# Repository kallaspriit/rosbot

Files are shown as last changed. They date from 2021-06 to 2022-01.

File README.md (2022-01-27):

# ROSBOT

ROS 2 based robot learning platform.

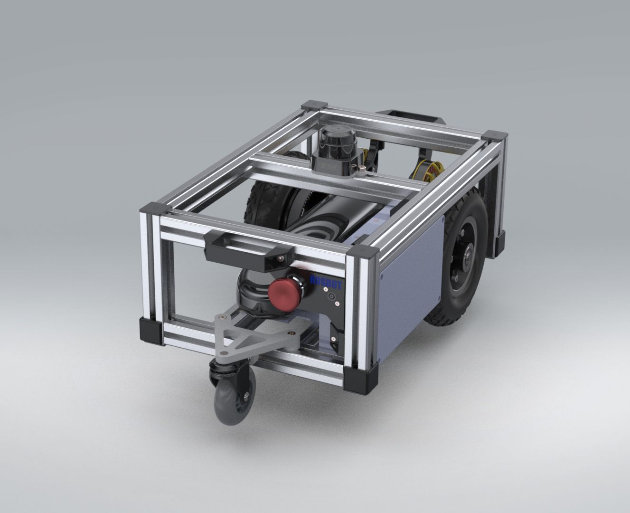
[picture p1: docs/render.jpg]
ROSBOT introductory video (https://www.youtube.com/watch?v=t-1GAfGHRLs)


_Click the image to video showing robot design and navigation in action_

## Bill of Materials

The BOM has not been designed for easy replication but most all used components and alternatives considered are there with respective links of where were they purchased so maybe it helps someone putting together a similar build :)

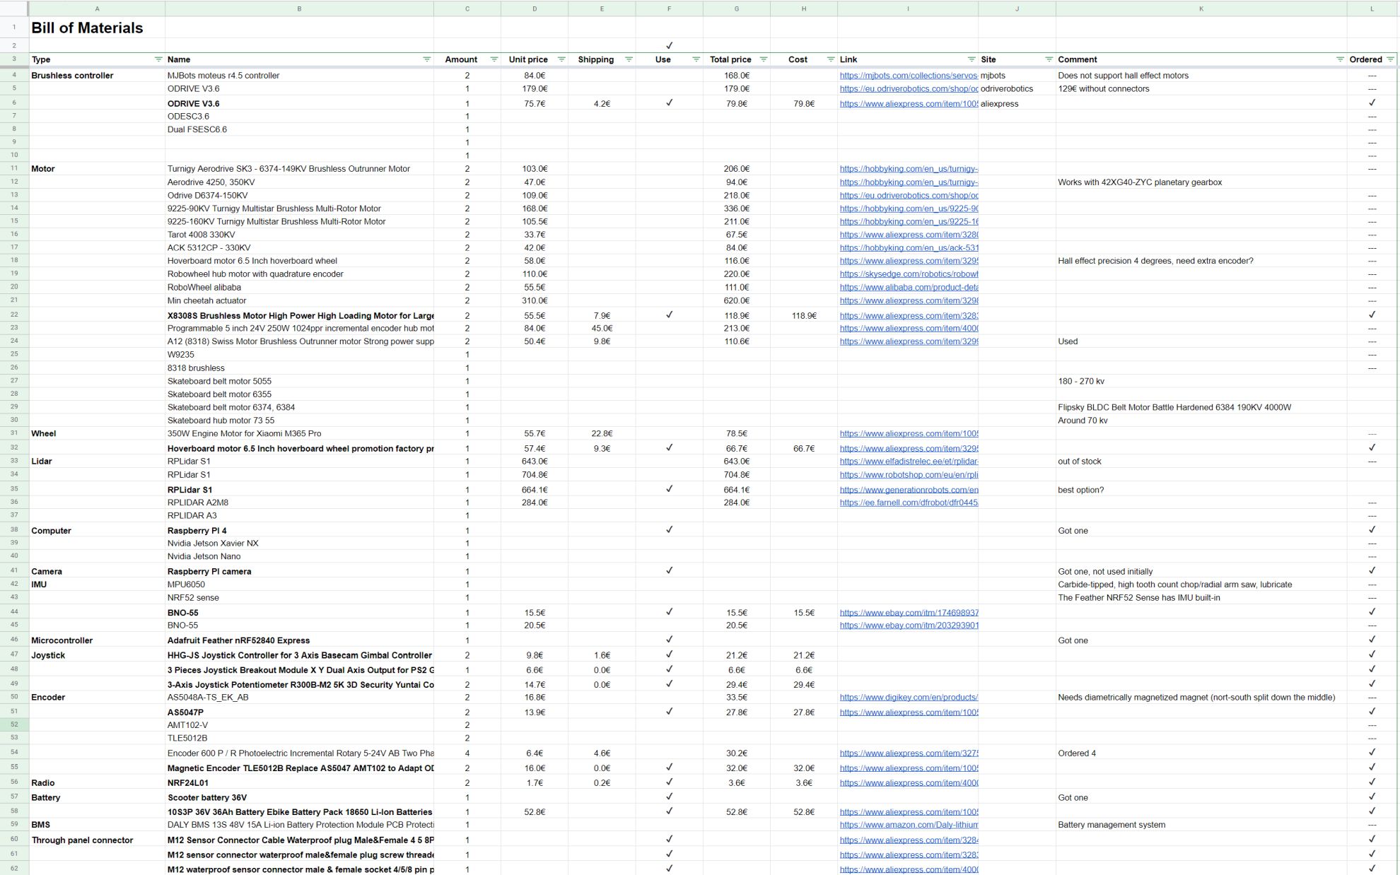
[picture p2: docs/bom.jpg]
Bill of materials (https://docs.google.com/spreadsheets/d/122i1k6gkCbc3--f4KSbXqv0-GW25-VVfwCtphQCVFGo/edit?usp=sharing)


_Click the image to open BOM_

## Run main rosbot/ros workspace

**Disclaimer**

_The following documentation is various commands and information that I've written over the time the robot was in development and everything is not up to date or relevant but maybe it helps someone._

- Add user to usb serial and input groups
  - `sudo usermod -a -G input ubuntu`
  - `sudo usermod -a -G dialout ubuntu`
  - `sudo usermod -a -G tty ubuntu`
- Build rosbot (on both the robot and the remote PC)
  - `cd ~/rosbot/ros` to open workspace
  - `rosdep install -i --from-path src --rosdistro foxy -y` to install dependencies
  - `git pull && colcon build` to pull changes and build workspace
- Launch rosbot on the robot
  - First build it if there have been any changes
  - Open new terminal
  - `cd ~/rosbot/ros` to open workspace
  - `. install/local_setup.bash` to load workspace overlay (on both robot and remote pc)
  - `ros2 launch odrive_bringup rosbot.launch.py` to launch rosbot (run on robot)
  - `ros2 launch odrive_bringup rviz.launch.py` to launch rviz (run on remote pc)
- Run joystick teleop
  - Open new terminal
  - `. install/local_setup.bash` to load workspace overlay
  - `ros2 launch teleop_twist_joy teleop.launch.py joy_config:='rosbot_xbox_bluetooth' cmd_vel:=/diff_drive_controller/cmd_vel_unstamped` to launch joystick teleop
  - Hold down left trigger (button 6) and use left and right joysticks to control speed and rotation
  - Hold down right trigger (button 7) for boost (faster movements)
- Launch odrive manual control (for testing only)
  - Open new terminal
  - `. install/local_setup.bash` to load workspace overlay
  - `ros2 launch odrive_bringup odrive.launch.py` to launch odrive test ()
  - `ros2 topic pub -r 100 /left_wheel_joint_velocity_controller/commands std_msgs/Float64MultiArray "data: [1]"`
  - `ros2 topic pub -r 100 /right_wheel_joint_velocity_controller/commands std_msgs/Float64MultiArray "data: [-1]"`
  - `ros2 launch teleop_twist_joy teleop.launch.py joy_config:='rosbot_xbox_bluetooth' cmd_vel:=/diff_drive_controller/cmd_vel_unstamped` to launch joystick teleop
  - Hold down left trigger (button 6) and use left and right joysticks to control speed and rotation
- Launch usb xbox joystick teleop that publishes to `/cmd_vel`
  - `ros2 launch teleop_twist_joy teleop.launch.py cmd_vel:=cmd_vel joy_config:=rosbot_xbox_usb`

## Debugging

- Debugging
- `ros2 topic echo /joint_states` to show joint states including velocity etc
- `ros2 topic echo /dynamic_joint_states` to show dynamic joint states including axis error etc
- `ros2 run tf2_tools view_frames.py` to generate `frames.pdf` frame tree
- `rqt` to open RQT, add plugins such as `Topics > Topic Monitor`
- `ros2 run xacro xacro ./src/rosbot_description/urdf/rosbot.urdf.xacro` to debug what's wrong with URDF file
- `ros2 run tf2_ros tf2_echo odom base_link` to verify transforms from odom to base_link
  - At time 1634580767.596875940
    - Translation: [6.986, -2.328, 0.000]
    - Rotation: in Quaternion [0.000, 0.000, -0.210, 0.978]
  - At time 1634580768.594622939
    - Translation: [7.108, -2.383, 0.000]
    - Rotation: in Quaternion [0.000, 0.000, -0.213, 0.977]

## Joystick teleop

- https://index.ros.org/p/teleop_twist_joy/github-ros2-teleop_twist_joy/
- https://github.com/ros2/teleop_twist_joy/tree/foxy/
- http://wiki.ros.org/joy
- https://github.com/medusalix/xow need xow to use xbox bluetooth controller
- Configure XOW to use xbox controller over bluetooth
  - `sudo apt install cabextract` to install dependencies
  - `git clone https://github.com/medusalix/xow`
  - `cd xow`
  - `make BUILD=RELEASE`
  - `sudo make install`
  - `sudo systemctl enable xow`
  - `sudo systemctl start xow`
  - `sudo systemctl kill -s SIGUSR1 xow` to enable XOW pairing mode (generally not needed)
- Disable ERTM
  - `sudoedit /sys/module/bluetooth/parameters/disable_ertm`
  - replace `N` with `Y`
  - reboot
- Restart bluetooth
  - `sudo service bluetooth restart`
  - `sudo rmmod btusb`
- Test controller
  - `jstest /dev/input/js0`
- Also disable ERTM permanently
  - https://www.addictivetips.com/ubuntu-linux-tips/xbox-one-controllers-over-bluetooth-linux/
  - `sudo apt install dkms git linux-headers-`uname -r``
  - `git clone https://github.com/atar-axis/xpadneo.git`
  - `cd xpadneo`
  - `sudo ./install.sh`
  - reboot
- Disable internal bluetooth when using dongle
  - `sudoedit /boot/firmware/usrcfg.txt`
  - add line `dtoverlay=disable-bluetooth`
  - reboot
  - check with `hciconfig -a` and `hcitool dev`
  - does not seem to actually work..
- Connect to bluetooth xbox controller using terminal (on robot)
  - https://simpleit.rocks/linux/shell/connect-to-bluetooth-from-cli/
  - https://raspberrypi.stackexchange.com/questions/114586/rpi-4b-bluetooth-unavailable-on-ubuntu-20-04
  - https://www.makeuseof.com/manage-bluetooth-linux-with-bluetoothctl/
  - `sudo apt install bluez pi-bluetooth joystick`
  - Append "include btcfg.txt" to `sudoedit /boot/firmware/usrcfg.txt`
  - reboot
  - `hciconfig -a` or `hcitool dev` (from bluez) to check for bluetooth devices
  - `bluetoothctl` to run interactive bluetooth controller
  - `scan on`
  - wait for xbox controller (make it pair by holding the pair button, starts to blink rapidly)
  - `trust XX:XX:XX:XX:XX:XX` to trust the controller
  - `connect XX:XX:XX:XX:XX:XX` to connect to the controller
  - `sudo chmod a+rw /dev/input/js0` to give everyone read-write permissions to joystick
  - `sudo chmod a+rw /dev/input/event4` to give everyone read-write permissions to joystick (sometimes it's one of eventX)
- If the joystick `/dev/input/eventX` does not have correct permissions then (this does not seem to actually work)
  - `sudo apt install input-utils` to install `lsinput` tool
  - `sudo lsinput` to get list of inputs, note the vendor and product of "Xbox Wireless Controller"
  - `sudoedit 80-xbox-controller.rules`
  - add `KERNEL=="event*", ATTRS{idProduct}=="02e0", ATTRS{idVendor}=="045e", MODE="0666"` etc that mathes vendor and product
- Test joystick from terminal
  - `sudo apt install joystick`
  - `jstest /dev/input/js0`
  - `ros2 run joy joy_enumerate_devices`
- Test joystick visually
  - `sudo apt install jstest-gtk`
  - `jstest-gtk`
- Test joystick messages
  - `ros2 topic echo /joy`
  - `ros2 topic echo /cmd_vel`
  - `ros2 topic echo /diff_drive_controller/cmd_vel_unstamped`

## Setup Gazebo simulator

- `sudo apt install ros-foxy-gazebo-ros-pkgs`

## Setup Raspberry PI UART

- https://askubuntu.com/questions/1254376/enable-uart-communication-on-pi4-ubuntu-20-04
- Create boot configuration backups
  - `cd /boot/firmware`
  - `sudo cp usrcfg.txt usrconfig.backup.txt`
  - `sudo cp cmdline.txt cmdline.backup.txt`
- Disable console UART
  - add `enable_uart=0` to `/boot/firmware/usrcfg.txt`
  - remove `console=serial0,115200` from `/boot/firmware/cmdline.txt`
- Disable the Serial Service which used the miniUART
  - `sudo systemctl stop serial-getty@ttyS0.service`
  - `sudo systemctl disable serial-getty@ttyS0.service`
  - `sudo systemctl mask serial-getty@ttyS0.service`
- UART Pins
  - Pin 8 TXD GPIO14
  - Pin 10 RXD GPIO15

## Setup ROS2 Navigation2 Nav2

- https://navigation.ros.org/getting_started/index.html
- Install dependencies
  - `sudo apt install ros-foxy-navigation2 ros-foxy-nav2-bringup ros-foxy-cartographer ros-foxy-cartographer-ros ros-foxy-robot-localization ros-foxy-slam-toolbox ros-foxy-gazebo-ros-pkgs ros-foxy-xacro ros-foxy-slam-toolbox`
  - `sudo apt install ros-foxy-turtlebot3*` for testing on remote pc only
- Slam toolbox on the robot
  - Use snap `slam-toolbox`
  - It has optimizations in it that make it about 10x faster
- Run mapping and navigation
  - `ros2 launch slam_toolbox online_async_launch.py` to launch slam toolbox mapper
  - `ros2 launch nav2_bringup navigation_launch.py` to run navigation2

## Run navigation2_tutorials

- Clone and build `https://github.com/ros-planning/navigation2_tutorials.git`
- launch robot `ros2 launch sam_bot_description display.launch.py`
- Launch usbteleop
  - Open new terminal
  - `cd ~/rosbot/ros`
  - `. install/local_setup.bash`
  - `ros2 launch teleop_twist_joy teleop.launch.py cmd_vel:=/demo/cmd_vel joy_config:=rosbot_xbox_usb`
  - or without the /demo in modified version
- Launch slam_toolbox
  - Open new terminal
  - `ros2 launch slam_toolbox online_async_launch.py`

## Setup Arduino

- Install Arduino IDE
- Add `https://www.adafruit.com/package_adafruit_index.json` to Arduino preferences additional boards URLs
- Install board `Adafruit nRF52`
- Install `pip3 install --user adafruit-nrfutil`
- Update bootloader
  - https://learn.adafruit.com/introducing-the-adafruit-nrf52840-feather/update-bootloader
  - Double press reset to enter DFU mode
- Install Micro-XRCE-DDS Agent
  - `git clone https://github.com/eProsima/Micro-XRCE-DDS-Agent.git`
  - `cd Micro-XRCE-DDS-Agent && git checkout foxy`
  - `mkdir build && cd build`
  - `source /opt/ros/dashing/setup.bash # to share libraries with ros2`
  - `cmake ..`
  - `make`
  - `sudo make install`
  - `sudo ldconfig /usr/local/lib/`

## Update cmake

- `cmake --version`
- `sudo apt update`
- `sudo apt install -y software-properties-common lsb-release`
- `wget -O - https://apt.kitware.com/keys/kitware-archive-latest.asc 2>/dev/null | gpg --dearmor - | sudo tee /etc/apt/trusted.gpg.d/kitware.gpg >/dev/null`
- `sudo apt-add-repository "deb https://apt.kitware.com/ubuntu/ $(lsb_release -cs) main"`
- `sudo apt update`
- `sudo apt install kitware-archive-keyring`
- `sudo rm /etc/apt/trusted.gpg.d/kitware.gpg`
- `sudo apt update`
- `sudo apt install cmake`
- `cmake --version`

## Build micro-ros on MBED

- https://github.com/micro-ROS/micro_ros_mbed
- `pip3 install catkin_pkg lark-parser empy colcon-common-extensions mbed-tools`
- `sudo apt install gcc-arm-none-eabi`
- clone repo and cd into it
- `mbed-tools deploy`
- `mbed-tools compile -m LPC1768 -t GCC_ARM -f`

## Install ROS

[Installation guide](https://docs.ros.org/en/foxy/Installation/Ubuntu-Install-Debians.html).

- Enable universe (probably not needed)
  - `sudo apt install software-properties-common`
  - `sudo add-apt-repository universe`
- Add repository
  - `sudo apt update && sudo apt install curl gnupg2 lsb-release`
  - `sudo curl -sSL https://raw.githubusercontent.com/ros/rosdistro/master/ros.key -o /usr/share/keyrings/ros-archive-keyring.gpg`
- Add repository to sources list
  - `echo "deb [arch=$(dpkg --print-architecture) signed-by=/usr/share/keyrings/ros-archive-keyring.gpg] http://packages.ros.org/ros2/ubuntu $(lsb_release -cs) main" | sudo tee /etc/apt/sources.list.d/ros2.list > /dev/null`
- Install ROS
  - `sudo apt update`
  - `sudo apt install ros-foxy-desktop`
- Install autocomplete
  - `sudo apt install -y python3-argcomplete`
- Add sourcing ROS to bashrc
  - `echo "source /opt/ros/foxy/setup.bash" >> ~/.bashrc`
- Add colcom_cd to bashrc
  - `echo "source /usr/share/colcon_cd/function/colcon_cd.sh" >> ~/.bashrc`
  - `echo "export _colcon_cd_root=~/ros2_install" >> ~/.bashrc`
- Check environment variables
  - `printenv | grep -i ROS`
- Set domain id (random number between 0-101 inclusive)
  - `echo "export ROS_DOMAIN_ID=<your_domain_id>" >> ~/.bashrc`
- Test ROS (open in separate terminals)
  - `ros2 run demo_nodes_cpp talker`
  - `ros2 run demo_nodes_py listener`
- Install ros bag for data recording/playback
  - `sudo apt-get install ros-galactic-ros2bag ros-galactic-rosbag2-storage-default-plugins`

## Install tools

- Install VSCode
  - `sudo snap install --classic code`

## Install TurtleSim

- Install
  - `sudo apt install ros-foxy-turtlesim`
- Check the package installed
  - `ros2 pkg executables turtlesim`
- Start turtlesim
  - `ros2 run turtlesim turtlesim_node`
- Start teleop to control the turtle
  - `ros2 run turtlesim turtle_teleop_key`

## Install RQT

- Install rqt
  - `sudo apt update`
  - `sudo apt install ~nros-foxy-rqt*`
- Run rqt
  - `rqt`
- Add service called
  - `select Plugins > Services > Service Caller`
  - Call `/spawn` with `x=1.0, y=1.0, name='turtle2'`
- Remap control to turtle 2
  - `ros2 run turtlesim turtle_teleop_key --ros-args --remap turtle1/cmd_vel:=turtle2/cmd_vel`
- Render rtq graph
  - `rqt_graph`
  - can also add to `rtq` by `Plugins > Introspection > Nodes Graph`

## ROS Command line

- Run node
  - `ros2 run turtlesim turtlesim_node`
  - `ros2 run turtlesim turtle_teleop_key`
  - `ros2 run turtlesim turtlesim_node --ros-args --log-level WARN` to run with custom log level
- List resources
  - `ros2 node list`
  - `ros2 topic list`
  - `ros2 topic list -t` to also show message types
  - `ros2 service list`
  - `ros2 service list -t` to also show service types
  - `ros2 action list`
  - `ros2 param list`
- Get node info
  - `ros2 node info /my_turtle`
- Show data published to topic
  - `ros2 topic echo /turtle1/cmd_vel` to see velocity commands
  - `ros2 topic echo /turtle1/pose` to see changing pose
- Get topic info
  - `ros2 topic info /turtle1/cmd_vel`
- Show messsage interface
  - `ros2 interface show geometry_msgs/msg/Twist`
- Publish message to topic
  - `ros2 topic pub <topic_name> <msg_type> '<args>'` where args is in YAML syntax
  - `ros2 topic pub --once /turtle1/cmd_vel geometry_msgs/msg/Twist "{linear: {x: 2.0, y: 0.0, z: 0.0}, angular: {x: 0.0, y: 0.0, z: 1.8}}"` publishes once
  - `ros2 topic pub --rate 1 /turtle1/cmd_vel geometry_msgs/msg/Twist "{linear: {x: 2.0, y: 0.0, z: 0.0}, angular: {x: 0.0, y: 0.0, z: 1.8}}"` publishes continuosly at 1Hz
- Show how often data is published to a topic
  - `ros2 topic hz /turtle1/pose`
- Get service type info
  - `ros2 service type <service_name>`
  - `ros2 service type /clear`
- Find service by type
  - `ros2 service find <type_name>`
  - `ros2 service find std_srvs/srv/Empty`
- Show service type structure
  - `ros2 interface show <type_name>.srv` where request and response structure is separated by ---
  - `ros2 interface show std_srvs/srv/Empty.srv`
  - `ros2 interface show turtlesim/srv/TeleportAbsolute.srv`
  - `ros2 interface show turtlesim/srv/Spawn`
- Call service
  - `ros2 service call <service_name> <service_type> <arguments>`
  - `ros2 service call /clear std_srvs/srv/Empty`
  - `ros2 service call /spawn turtlesim/srv/Spawn "{x: 2, y: 2, theta: 0.2, name: ''}"`
- Get param list
  - `ros2 param list`
- Get param value
  - `ros2 param get <node_name> <parameter_name>`
  - `ros2 param get /turtlesim background_g`
- Set param value
  - `ros2 param set <node_name> <parameter_name> <value>`
  - `ros2 param set /turtlesim background_r 150`
- Dump node parameters
  - `ros2 param dump <node_name>`
  - `ros2 param dump /turtlesim`
- Start node using parameters from dumped file
  - `ros2 run <package_name> <executable_name> --ros-args --params-file <file_name>`
  - `ros2 run turtlesim turtlesim_node --ros-args --params-file ./turtlesim.yaml`
- Get list of node actions
  - `ros2 node info /turtlesim`
  - `ros2 node info /teleop_turtle`
- Get list of all actions
  - `ros2 action list`
  - `ros2 action list -t` to also show action types
- Get action info
  - `ros2 action info /turtle1/rotate_absolute`
- Get action interface info
  - `ros2 interface show turtlesim/action/RotateAbsolute`
- Call action
  - `ros2 action send_goal <action_name> <action_type> <values>`
  - `ros2 action send_goal /turtle1/rotate_absolute turtlesim/action/RotateAbsolute "{theta: 1.57}"`
  - `ros2 action send_goal /turtle1/rotate_absolute turtlesim/action/RotateAbsolute "{theta: 3.14}" --feedback` to also get feedback
- Run rqt console
  - `ros2 run rqt_console rqt_console`
- Start node
  - `ros2 run rqt_console rqt_console`
- Launch launch file
  - `ros2 topic pub -r 1 /turtlesim1/turtle1/cmd_vel geometry_msgs/msg/Twist "{linear: {x: 2.0, y: 0.0, z: 0.0}, angular: {x: 0.0, y: 0.0, z: -1.8}}"`
- Record topic to bag
  - `ros2 bag record <topic_name>` to record a topic
  - `ros2 bag record /turtle1/cmd_vel`
  - `ros2 bag record -o subset /turtle1/cmd_vel /turtle1/pose` top choose filename `subset` and record multiple topics
- Get bag info
  - `ros2 bag info <bag_file_name>`
  - `ros2 bag info subset`
- Play back bag recording
  - `ros2 bag play <bag_file_name>`
  - `ros2 bag play subset`

## Example launch file

Starts two turtlesim nodes with different namespace names and a mimic node that makes the second turtle mimic first one.

```py
from launch import LaunchDescription
from launch_ros.actions import Node

def generate_launch_description():
    return LaunchDescription([
        Node(
            package='turtlesim',
            namespace='turtlesim1',
            executable='turtlesim_node',
            name='sim'
        ),
        Node(
            package='turtlesim',
            namespace='turtlesim2',
            executable='turtlesim_node',
            name='sim'
        ),
        Node(
            package='turtlesim',
            executable='mimic',
            name='mimic',
            remappings=[
                ('/input/pose', '/turtlesim1/turtle1/pose'),
                ('/output/cmd_vel', '/turtlesim2/turtle1/cmd_vel'),
            ]
        )
    ])
```

## TMUX terminal splitter

- Install
  - `sudo apt install tmux`
- Start
  - `tmux`
- Split terminal
  - horizonal `ctrl+b %`
  - vertical `ctrl+b "`
- Manage windows
  - create `ctrl+b c`
  - close `exit`
  - rename `ctrl+b ,`
- Navigate
  - between panels `ctrl+b ARROWS`
  - between windows `ctrl+b N` where first N=0, second N=1 etc

## Base ros setup

https://docs.ros.org/en/foxy/Installation/Ubuntu-Install-Binary.html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

/opt/ros/foxy

- sudo apt install -y python3-rosdep
- rosdep update
- rosdep install --from-paths /opt/ros/foxy/share --ignore-src --rosdistro foxy -y --skip-keys "console_bridge fastcdr fastrtps osrf_testing_tools_cpp poco_vendor rmw_connextdds rti-connext-dds-5.3.1 tinyxml_vendor tinyxml2_vendor urdfdom urdfdom_headers"

## Creating workspace

https://docs.ros.org/en/foxy/Tutorials/Workspace/Creating-A-Workspace.html

- mkdir -p ~/dev_ws/src
- cd ~/dev_ws/src
- git clone https://github.com/ros/ros_tutorials.git -b foxy-devel
- rosdep install -i --from-path src --rosdistro foxy -y
- colcon build
- open new terminal to source overlay
- cd ~/dev_ws

## Build package

- create workspace directory `mkdir ros2_ws` etc
- create "src" in this directory
- copy the library/package into src
- `rosdep install -i --from-path src --rosdistro foxy -y` to install dependencies
- cd back to workspace and run `colcon build` to build the package

## Teleop robot controller

- https://github.com/ros-teleop/teleop_tools/tree/foxy-devel
- https://ubuntu.com/blog/the-teleop_tools-arrive-in-ros-2-dashing
- `ros2 run mouse_teleop mouse_teleop`
- `ros2 run mouse_teleop mouse_teleop --ros-args -r holonomic:=true`
- `ros2 topic echo /mouse_vel`

## Run experiments/test_odrive_ros2 package

- `cd ~/rosbot/experiments/test_odrive_ros2/`
- `ros2 run odrive_ros2 odrive_node`
- `ros2 service call /connect_odrive std_srvs/srv/Trigger`
- `ros2 service call /request_state odrive_interfaces/srv/AxisState "{axis: 0, state: 8}"` (not needed if started in closed loop control)
- `ros2 service call /velocity_cmd odrive_interfaces/srv/VelocityControl "{axis: 0, turns_s: 0.5}"`
- `ros2 topic echo /barrery_percentage` (typo.. and not sure of the format, returns something like 3.5)
- `ros2 topic echo /joint_state`

## RVIZ2

- https://www.stereolabs.com/docs/ros2/rviz2/

# Run experiments/test_odrive_ros2_control package

- https://ros-controls.github.io/control.ros.org/getting_started.html
- https://github.com/ros-controls/ros2_control
- https://github.com/ros-controls/ros2_controllers
- https://github.com/ros-controls/ros2_control_demos
- https://github.com/ros-controls/ros2_controllers/tree/master/diff_drive_controller
- http://wiki.ros.org/urdf
- https://github.com/ros-controls/roadmap/blob/master/design_drafts/components_architecture_and_urdf_examples.md
- https://github.com/ros-controls/ros2_control_demos/blob/master/ros2_control_demo_bringup/config/diffbot_diff_drive_controller.yaml
- https://github.com/ros-controls/ros2_control_demos/tree/master/ros2_control_demo_description/diffbot_description
- https://github.com/ros-controls/ros2_control_demos/blob/master/ros2_control_demo_bringup/launch/diffbot_system.launch.py
- https://ros-controls.github.io/control.ros.org/ros2_control/ros2controlcli/doc/userdoc.html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 CLI
- `cd ~/rosbot/experiments/test_odrive_ros2_control/`
- `sudo apt install ros-foxy-ros2-control ros-foxy-ros2-controllers`
- `ros2 launch odrive_bringup odrive.launch.py enable_joint1:=true`
- `ros2 topic pub -r 100 /joint0_velocity_controller/commands std_msgs/Float64MultiArray "data: [1]"`
- `ros2 topic pub -r 100 /joint1_velocity_controller/commands std_msgs/Float64MultiArray "data: [-1]"`

## Run ros2_control_demos

- copy repo https://github.com/ros-controls/ros2_control_demos
- create workspace folder, move demo repo folders under `src`
- `cd ros2_control_demos/`
- `rosdep install -i --from-path src --rosdistro foxy -y`
- `colcon build`
- open new terminal
- `cd ros2_control_demos/`
- `. install/local_setup.bash`
- `ros2 launch ros2_control_demo_bringup diffbot_system.launch.py start_rviz:=true`
- `ros2 control list_hardware_interfaces` to list ros control hardware interfaces
- `ros2 control list_controllers` to list ros control controllers
- publish velocity command

```
ros2 topic pub --rate 30 /diff_drive_controller/cmd_vel_unstamped geometry_msgs/msg/Twist "linear:
 x: 0.7
 y: 0.0
 z: 0.0
angular:
 x: 0.0
 y: 0.0
 z: 1.0"
```

- control with mouse_teleop, remapping /mouse_vel to /diff_drive_controller/cmd_vel_unstamped
- `ros2 run mouse_teleop mouse_teleop --ros-args -r /mouse_vel:=/diff_drive_controller/cmd_vel_unstamped`

## Open VSCode from Ubuntu explorer context menu

- Run the following in terminal
- `wget -qO- https://raw.githubusercontent.com/cra0zy/code-nautilus/master/install.sh | bash`

## Configure ssh

- `ssh-keygen -t rsa` to create ssh key in `~/.ssh` if not already present
- `cat ~/.ssh/id_rsa.pub` to get public key from computer that wants to access robot
- add the public key to robot's `~/.ssh/authorized_keys` file
- create `~/.ssh/config` file on the remote computer with contents like

```
Host rosbot
    HostName rosbot
    User ubuntu
```

- `ssh rosbot` to open ssh connection to robot using the configuration and ssh key

## Create package

cd ~/dev_ws/src
ros2 pkg create --build-type ament_cmake <package_name>
ros2 pkg create --build-type ament_cmake --node-name my_node my_package
ros2 pkg create --build-type ament_cmake --node-name talker test_chat

## Develop C++

https://github.com/ros2/rclcpp
http://docs.ros2.org/latest/api/rclcpp/
http://wiki.ros.org/std_msgs

## Develop nodejs

https://github.com/RobotWebTools/rclnodejs
https://github.com/RobotWebTools/rclnodejs-cli
http://robotwebtools.org/rclnodejs/docs/0.20.0/index.html
https://github.com/RobotWebTools/rclnodejs/tree/develop/example
npx generate-ros-messages

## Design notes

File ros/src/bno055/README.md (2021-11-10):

# A BNO05 ROS2 Package 

## Description
A ROS2 driver for the sensor IMU Bosch BNO055.

This repo was based off of [Michael Drwiega's work on the Bosch IMU Driver for ROS 1](https://github.com/mdrwiega/bosch_imu_driver)

---
## Wiring Guide

### Selecting Connection Type

The default mode is I2C.
To select UART mode connect the `3.3V` pin to the `PS1` pin.

### CP2104 USB-to-UART Bridge

When using a CP2104 USB-to-UART Bridge:

| BNO055 | CP2104 Friend |
| --- | --- |
| Vin | 5V |
| GND | GND |
| SDA | RXD |
| SCL | TXD |

**NOTE: on the CP2104 the pins above refer to the FTDI pins at the opposite end from the USB connector

---
## ROS Node Parameters

To configure with your own settings please adjust the [node parameter file](bno055/params/bno055_params.yaml) and pass it
as an argument when starting the node:

```
ros2 run bno055 bno055 --ros-args --params-file ./src/bno055/bno055/params/bno055_params.yaml
```

### UART Connection

- **connection_type=uart**: Defines UART as sensor connection type; default='uart'
- **uart_port**: The UART port to use; default='/dev/ttyUSB0'
- **uart_baudrate**: The baud rate to use; default=115200
- **uart_timeout**: The timeout for UART transmissions in seconds to use; default=0.1
  
### Sensor Configuration

- **frame_id**: coordinate frame id of sensor default='bno055'
- **baudrate**: baudrate of sensor default=115200
- **data_query_frequency**: frequency (HZ) to read and publish data from sensor; default=100 Hz
- **calib_status_frequency**: frequency (HZ) to read and publish calibration status data from sensor; default=0.1 Hz
- **placement_axis_remap**: The sensor placement configuration (Axis remapping) defines the position and orientation of the sensor mount.
See Bosch BNO055 datasheet section "Axis Remap" for valid positions: "P0", "P1" (default), "P2", "P3", "P4", "P5", "P6", "P7".   

### ROS Topic Prefix

- **ros_topic_prefix**: ROS topic prefix to be used. Will be prepended to the default topic names (see below). Default="bno055/"

---
## ROS Topics

ROS topics published by this ROS2 Node: 

  - **bno055/imu** [(sensor_msgs/Imu)](http://docs.ros.org/api/sensor_msgs/html/msg/Imu.html)
  - **bno055/imu_raw** [(sensor_msgs/Imu)](http://docs.ros.org/api/sensor_msgs/html/msg/Imu.html)
  - **bno055/temp** [(sensor_msgs/Temperature)](http://docs.ros.org/api/sensor_msgs/html/msg/Temperature.html); The sensor's ambient temperature
  - **bno055/mag** [(sensor_msgs/MagneticField)](http://docs.ros.org/api/sensor_msgs/html/msg/MagneticField.html)
  - **bno055/calib_status** [(std_msgs/String)](http://docs.ros.org/en/api/std_msgs/html/msg/String.html) : 
  Sensor Calibration Status as JSON string - e.g. `{"sys": 3, "gyro": 3, "accel": 0, "mag": 3}`

While _bno055_ is the default ROS topic prefix, it can be configured by following the directions above.

---
  
## Development Workspace Setup

### On a Remote Device
Setup of a ROS2 workspace & IDE for a remote device (for example Raspberry Pi):

#### Clone & Build

Create a ROS2 [workspace](https://index.ros.org/doc/ros2/Tutorials/Workspace/Creating-A-Workspace/) on your remote device - for instance `~/ros2_ws`

Make sure you sourced your ROS2 installation (underlay).

Then clone the project into your workspace's src directory:

    cd ~/ros2_ws/src
    git clone https://github.com/flynneva/bno055.git
    
Perform a build of your workspace
    
    cd ~/ros2_ws
    colcon build

#### Integrate in your IDE

In order to work with the sources in your remote workspace and to integrate them in your IDE, use `sshfs`:

    sudo apt-get install sshfs
    sudo modprobe fuse

Create a IDE project directory and mount the remote ROS2 workspace:

    mkdir -p ~/projects/bno055/ros2_ws
    sshfs ubuntu@192.168.2.153:~/ros2_ws ~/projects/bno055/ros2_ws
    
Create a new project in your IDE from existing sources in `~/projects/bno055/ros2_ws`. 
You can now manipulate the remote ROS2 workspace using your local IDE (including git operations). 

### Running the ROS2 node
Run the `bno055` ROS2 node with default parameters:

    # source your local workspace (overlay) in addition to the ROS2 sourcing (underlay):
    source ~/ros2_ws/install/setup.sh
    # run the node:
    ros2 run bno055 bno055
    
Run with customized parameter file:

    ros2 run bno055 bno055 --ros-args --params-file ./src/bno055/bno055/params/bno055_params.yaml
    
### Performing flake8 Linting

To perform code linting with [flake8](https://gitlab.com/pycqa/flake8) just perform:

    cd ~/ros2_ws/src/bno055
    ament_flake8

See [www.flake8rules.com](https://www.flake8rules.com/) for more detailed information about flake8 rules.

**Note:** we take advantage of [flake8's noqa mechanisim](https://flake8.pycqa.org/en/3.1.1/user/ignoring-errors.html) to selectively ignore some errors. Just search for `# noqa:` in the source code to find them.

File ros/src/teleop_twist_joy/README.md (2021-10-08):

ros2/teleop_twist_joy
================

# Overview
The purpose of this package is to provide a generic facility for tele-operating Twist-based ROS2 robots with a standard joystick. 
It converts joy messages to velocity commands.

This node provides no rate limiting or autorepeat functionality. It is expected that you take advantage of the features built into [joy](https://index.ros.org/p/joy/github-ros-drivers-joystick_drivers/#foxy) for this.

## Executables
The package comes with the `teleop_node` that republishes `sensor_msgs/msg/Joy` messages as scaled `geometry_msgs/msg/Twist` messages.

## Subscribed Topics
- `joy (sensor_msgs/msg/Joy)`
  - Joystick messages to be translated to velocity commands.

## Published Topics
- `cmd_vel (geometry_msgs/msg/Twist)`
  - Command velocity messages arising from Joystick commands.

## Parameters
- `require_enable_button (bool, default: true)`
  - Whether to require the enable button for enabling movement.

- `enable_button (int, default: 0)`
  - Joystick button to enable regular-speed movement.
  
- `enable_turbo_button (int, default: -1)`
  - Joystick button to enable high-speed movement (disabled when -1).

- `axis_linear.<axis>`
  - Joystick axis to use for linear movement control.
  - `axis_linear.x (int, default: 5)`
  - `axis_linear.y (int, default: -1)`
  - `axis_linear.z (int, default: -1)`

- `scale_linear.<axis>`
  - Scale to apply to joystick linear axis for regular-speed movement.
  - `scale_linear.x (double, default: 0.5)`
  - `scale_linear.y (double, default: 0.0)`
  - `scale_linear.z (double, default: 0.0)`

- `scale_linear_turbo.<axis>`
  - Scale to apply to joystick linear axis for high-speed movement.
  - `scale_linear_turbo.x (double, default: 1.0)`
  - `scale_linear_turbo.y (double, default: 0.0)`
  - `scale_linear_turbo.z (double, default: 0.0)`

- `axis_angular.<axis>`
  - Joystick axis to use for angular movement control.
  - `axis_angular.yaw (int, default: 2)`
  - `axis_angular.pitch (int, default: -1)`
  - `axis_angular.roll (int, default: -1)`
  
- `scale_angular.<axis>`
  - Scale to apply to joystick angular axis.
  - `scale_angular.yaw (double, default: 0.5)`
  - `scale_angular.pitch (double, default: 0.0)`
  - `scale_angular.roll (double, default: 0.0)`
  
- `scale_angular_turbo.<axis>`
  - Scale to apply to joystick angular axis for high-speed movement.
  - `scale_angular_turbo.yaw (double, default: 1.0)`
  - `scale_angular_turbo.pitch (double, default: 0.0)`
  - `scale_angular_turbo.roll (double, default: 0.0)`

# Usage

## Install
For most users building from source will not be required, execute `apt-get install ros-<rosdistro>-teleop-twist-joy` to install.

## Run
A launch file has been provided which has three arguments which can be changed in the terminal or via your own launch file.
To configure the node to match your joystick a config file can be used. 
There are several common ones provided in this package (atk3, ps3-holonomic, ps3, xbox, xd3), located here: https://github.com/ros2/teleop_twist_joy/tree/eloquent/config.

PS3 is default, to run for another config (e.g. xbox) use this:
````
ros2 launch teleop_twist_joy teleop.launch.py joy_config:='xbox'
````

__Note:__ this launch file also launches the `joy` node so do not run it separately.

## Arguments
- `joy_config (string, default: 'ps3')`
  - Config file to use
- `joy_dev (string, default: 'dev/input/js0')`
  - Joystick device to use
- `config_filepath (string, default: '/opt/ros/<rosdistro>/share/teleop_twist_joy/config/' + LaunchConfig('joy_config') + '.config.yaml')`
  - Path to config files

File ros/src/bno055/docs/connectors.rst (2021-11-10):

connectors
====================================

.. automodule:: bno055.connectors.Connector
    :members:
    :show-inheritance:

.. automodule:: bno055.connectors.uart
    :members:
    :show-inheritance:

.. automodule:: bno055.connectors.i2c
    :members:
    :show-inheritance:

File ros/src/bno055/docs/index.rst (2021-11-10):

.. bno055 documentation master file, created by
   sphinx-quickstart on Mon Feb  8 19:58:23 2021.
   You can adapt this file completely to your liking, but it should at least
   contain the root `toctree` directive.

Welcome
==================================

A ROS2 driver for the sensor IMU Bosch BNO055.

.. toctree::
   :maxdepth: 4
   :caption: Contents:

   bno055
   connectors
   error_handling
   params
   sensor
   registers 

Indices and tables
==================

* :ref:`genindex`
* :ref:`modindex`
* :ref:`search`

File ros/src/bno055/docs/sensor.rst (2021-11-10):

sensor
====================================

.. automodule:: bno055.sensor.SensorService
    :members:

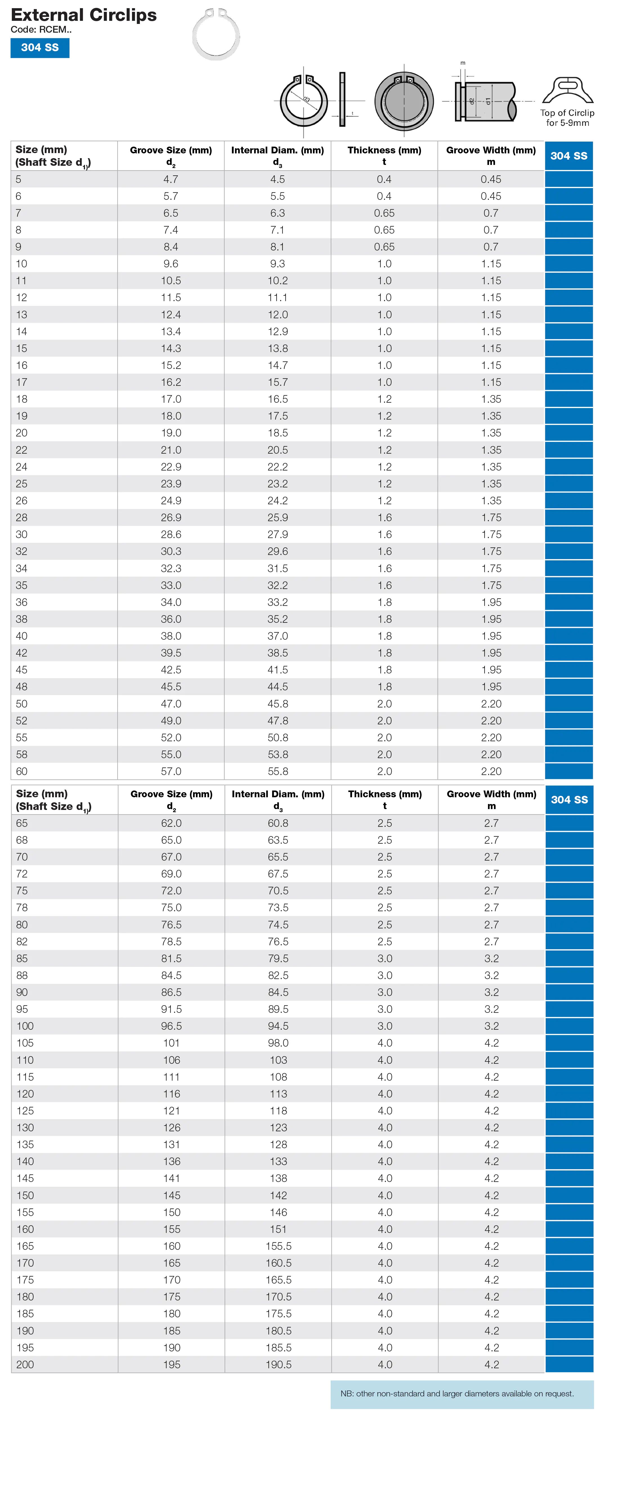
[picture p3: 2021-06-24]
docs/circlips.jpg

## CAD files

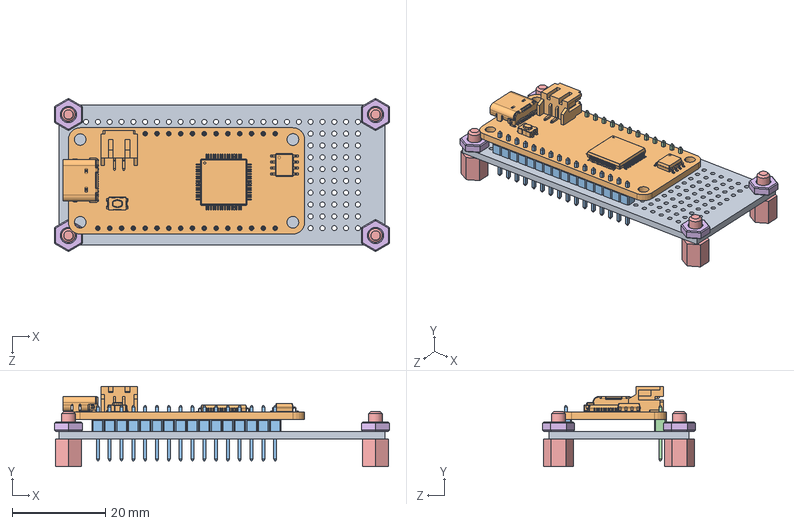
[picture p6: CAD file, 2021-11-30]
solidworks/adafruit-feather/feather-with-protoboard.SLDASM
72.0 x 17.3 x 32.9 mm
protoboard-70x30
adafruit-feather
16-Pin Header - Male - 2.54mm(2)^16-Pin Header - Male - 2.54mm(2)_pinheader-2.54mm-male-16
12-Pin Header - Male - 2.54mm(2)^12-Pin Header - Male - 2.54mm(2)_pinheader-2.54mm-male-12
spacer-nylon-6mm-M3 x 4
nut-M3 x 4

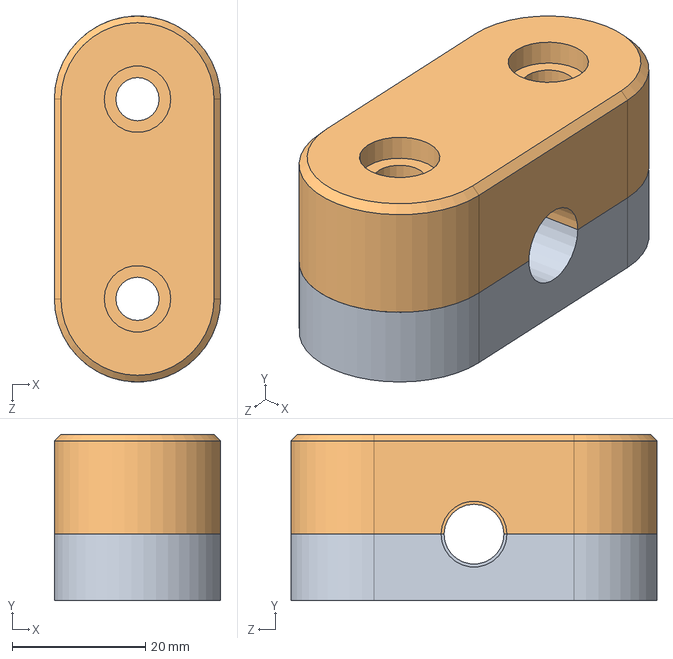
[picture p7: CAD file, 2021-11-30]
solidworks/axle-mount/axle-mount.SLDASM
25.0 x 25.0 x 55.0 mm
axle-mount-bottom
axle-mount-top

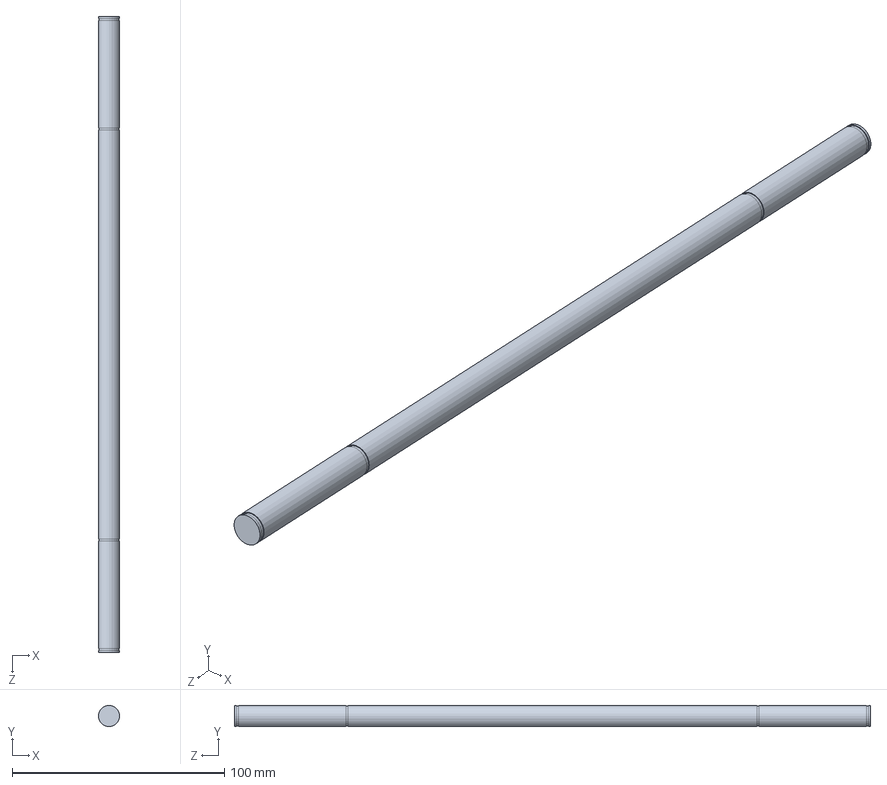
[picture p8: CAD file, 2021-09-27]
solidworks/axle/main-wheels-axle.SLDPRT
10.0 x 10.0 x 300.0 mm

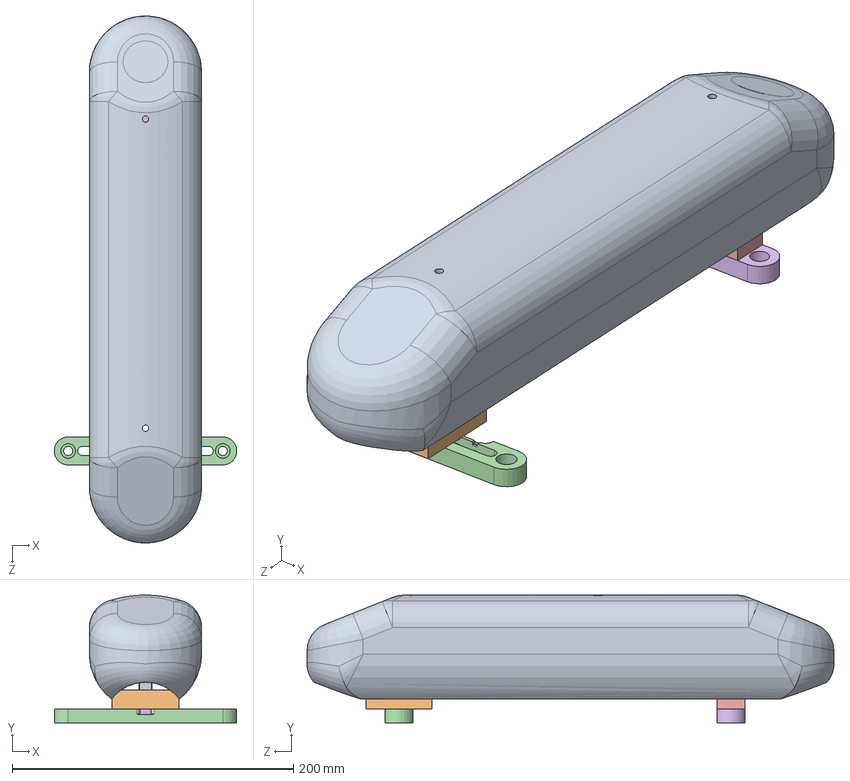
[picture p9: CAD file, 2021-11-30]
solidworks/battery/ninebot-battery.SLDASM
129.9 x 91.0 x 375.0 mm
ninebot-battery
ninebot-battery-connector
ninebot-battery-support
ninebot-battery-mount
ninebot-battery-base
ninebot-battery-base-mount

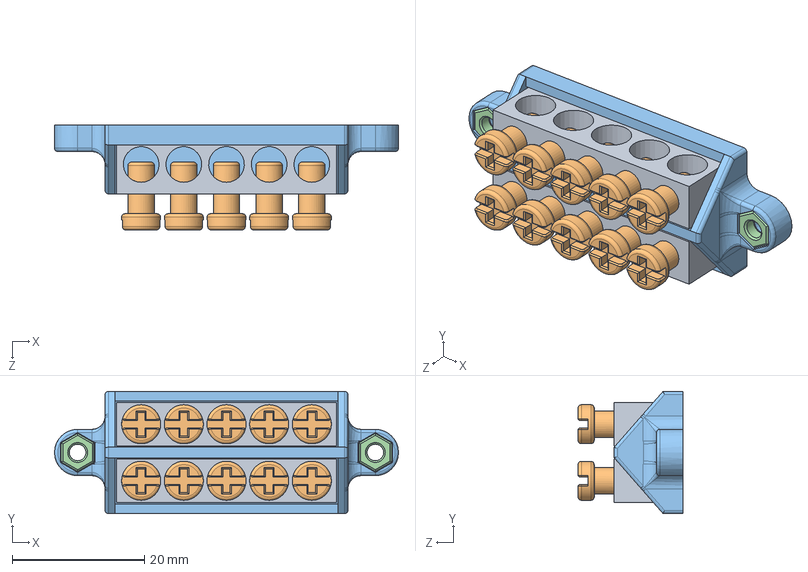
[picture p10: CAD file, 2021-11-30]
solidworks/bus-bar/bus-bar-dual-with-mount.SLDASM
52.0 x 18.5 x 15.9 mm
bus-bar-body x 2
bus-bar-screw x 10
bus-bar-dual-mount
nut-M2.5 x 2

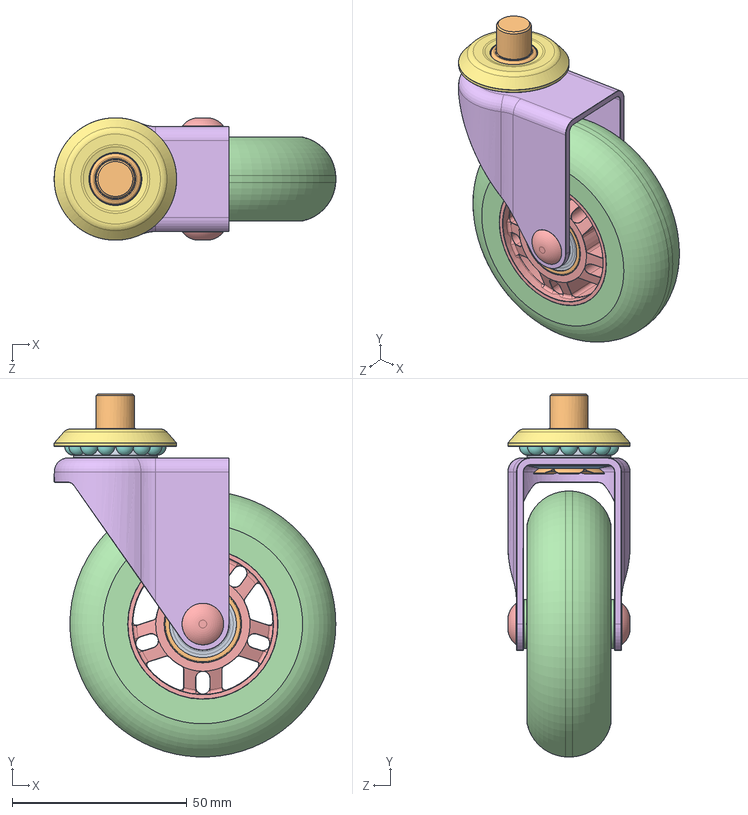
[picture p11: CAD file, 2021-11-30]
solidworks/caster-wheel/caster-wheel.SLDASM
80.5 x 103.8 x 35.0 mm
SKF_608-2Z_PART1^SKF_608-2Z_OCW_00(2)_caster-wheel x 2
SKF_608-2Z_PART2^SKF_608-2Z_OCW_00(2)_caster-wheel x 2
SKF_608-2Z_PART3^SKF_608-2Z_OCW_00(2)_caster-wheel x 14
OCW_01^OCW_00(2)_caster-wheel
OCW_02^OCW_00(2)_caster-wheel
OCW_03^OCW_00(2)_caster-wheel
OCW_05^OCW_00(2)_caster-wheel
OCW_04^OCW_00(2)_caster-wheel x 14
OCW_06^OCW_00(2)_caster-wheel
OCW_07^OCW_00(2)_caster-wheel
OCW_08^OCW_00(2)_caster-wheel
OCW_10^OCW_00(2)_caster-wheel x 2
OCW_11^OCW_00(2)_caster-wheel

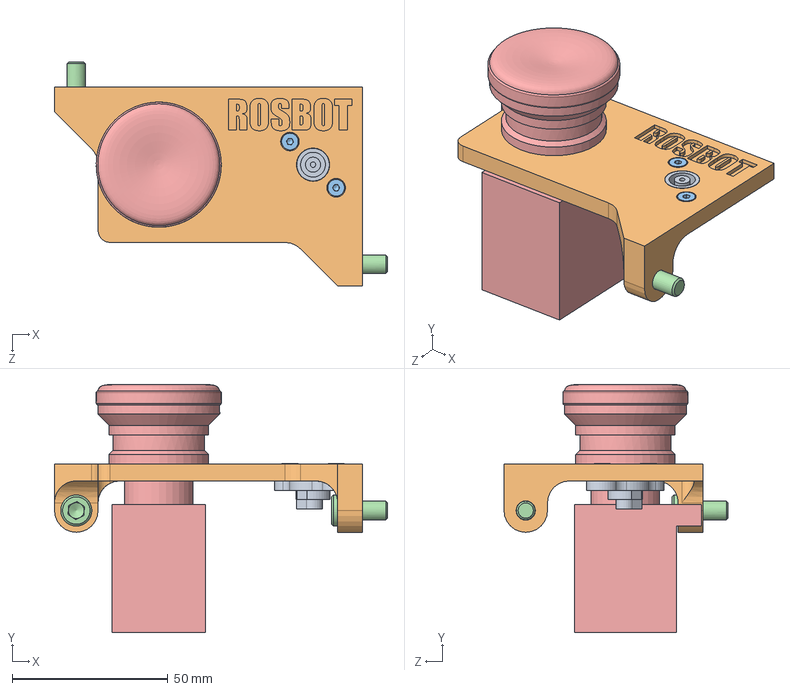
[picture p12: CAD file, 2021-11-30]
solidworks/charge-port/charge-port.SLDASM
107.0 x 79.7 x 72.0 mm
charge-port
charge-port-mount
socket countersunk head screw_am x 2
socket head cap screw_am x 2
e-stop

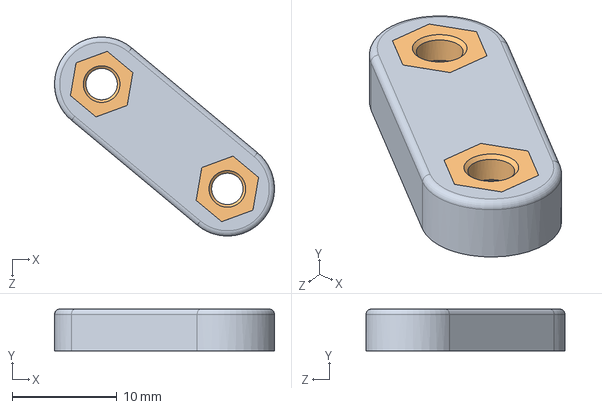
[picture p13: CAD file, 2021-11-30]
solidworks/corner-mount/corner-mount-backing.SLDASM
21.0 x 4.00 x 19.0 mm
corner-mount-backing
nut-M3 x 2

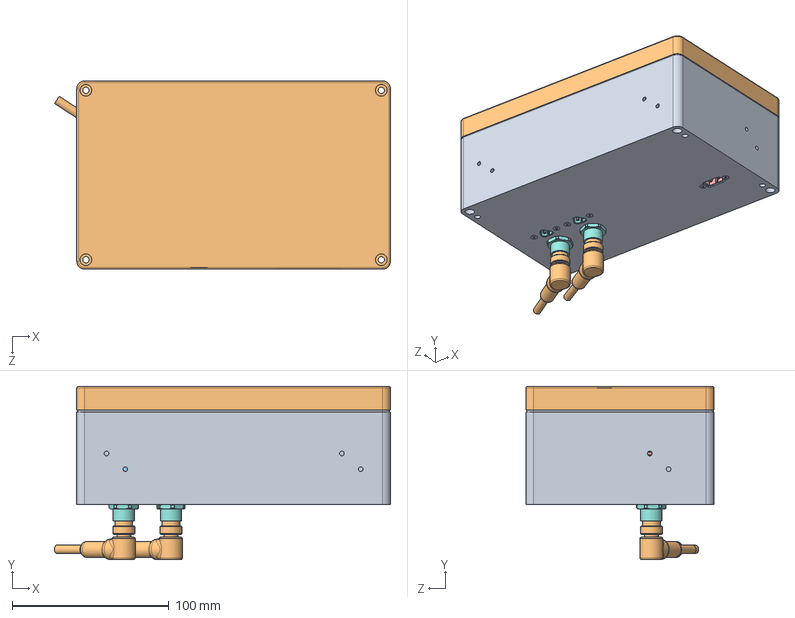
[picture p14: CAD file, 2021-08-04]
solidworks/electronics-box/electronics-box.SLDASM
214.2 x 110.4 x 120.1 mm
multicomp-G373-bottom
Board^odrive
CAP_Alum_Elec_Size_G^C15_PCB_v3.5(2)_odrive_v3.5
CAP_Alum_Elec_Size_G^C14_PCB_v3.5(2)_odrive_v3.5
CAP_Alum_Elec_Size_G^C13_PCB_v3.5(2)_odrive_v3.5
CAP_Alum_Elec_Size_G^C12_PCB_v3.5(2)_odrive_v3.5
CAP_Alum_Elec_Size_G^C11_PCB_v3.5(2)_odrive_v3.5
CAP_Alum_Elec_Size_G^C16_PCB_v3.5(2)_odrive_v3.5
CAP_Alum_Elec_Size_G^C17_PCB_v3.5(2)_odrive_v3.5
CAP_Alum_Elec_Size_G^C18_PCB_v3.5(2)_odrive_v3.5
spacer-nylon-12mm-M3 x 4
50w-resistor
variable-regulator
socket countersunk head screw_am x 8
M12-female-through-panel x 2
M12-connector-nut x 2
M12-male-cable x 2
M2.5 Nut v1^Amass XT60E1-M (2)_XT60E1-M
M2.5 Nut v1 (1)^Amass XT60E1-M (2)_XT60E1-M
Amass XT60E1-M^Amass XT60E1-M (2)_XT60E1-M
bolt-countersunk-M2.5 x 6
MT30-M-mount x 2
MT30-M-female x 2
nut-M2.5 x 4

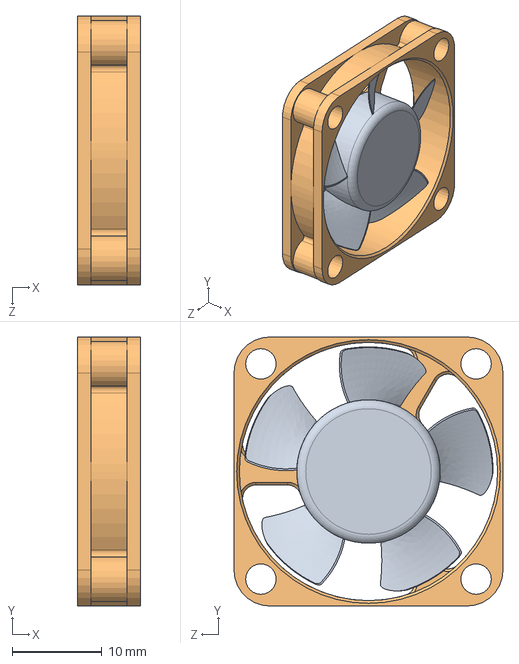
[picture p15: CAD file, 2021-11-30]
solidworks/fan/fan-30mm.SLDASM
7.00 x 30.0 x 30.0 mm
Component1^Fan 30mm(2)_fan-30mm
Fan 30mm(2)^Fan 30mm(2)_fan-30mm

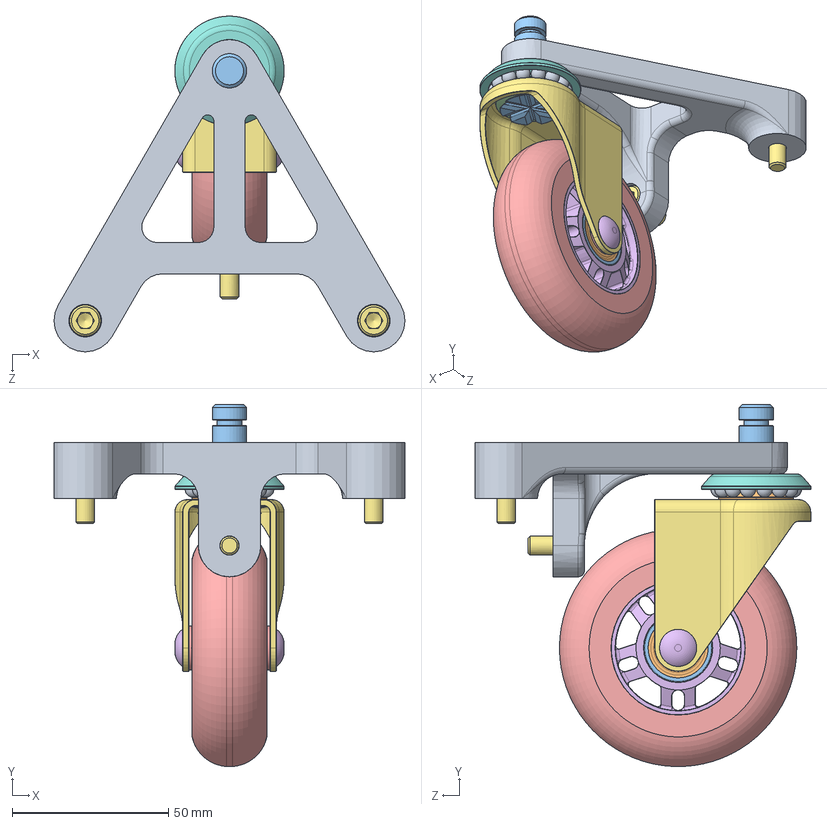
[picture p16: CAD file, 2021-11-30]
solidworks/front-wheel/front-wheel-center.SLDASM
112.4 x 115.9 x 107.5 mm
front-wheel-center-mount
SKF_608-2Z_PART1^SKF_608-2Z_OCW_00(2)_caster-wheel x 2
SKF_608-2Z_PART2^SKF_608-2Z_OCW_00(2)_caster-wheel x 2
SKF_608-2Z_PART3^SKF_608-2Z_OCW_00(2)_caster-wheel x 14
OCW_01^OCW_00(2)_caster-wheel
OCW_02^OCW_00(2)_caster-wheel
OCW_03^OCW_00(2)_caster-wheel
OCW_05^OCW_00(2)_caster-wheel
OCW_04^OCW_00(2)_caster-wheel x 14
OCW_06^OCW_00(2)_caster-wheel
OCW_07^OCW_00(2)_caster-wheel
OCW_08^OCW_00(2)_caster-wheel
OCW_10^OCW_00(2)_caster-wheel x 2
OCW_11^OCW_00(2)_caster-wheel
socket head cap screw_am x 3

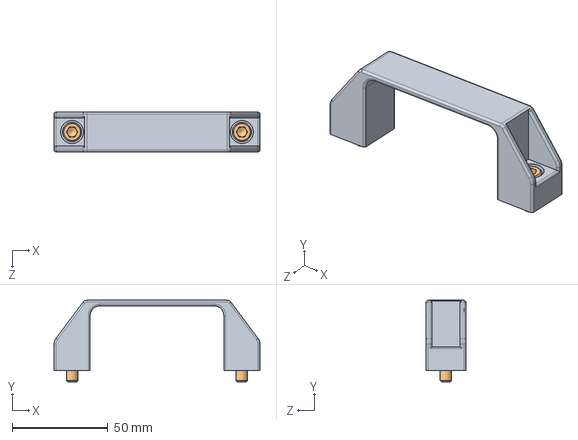
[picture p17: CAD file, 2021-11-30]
solidworks/handle/handle.SLDASM
107.3 x 42.5 x 20.6 mm
handle
socket head cap screw_am x 2

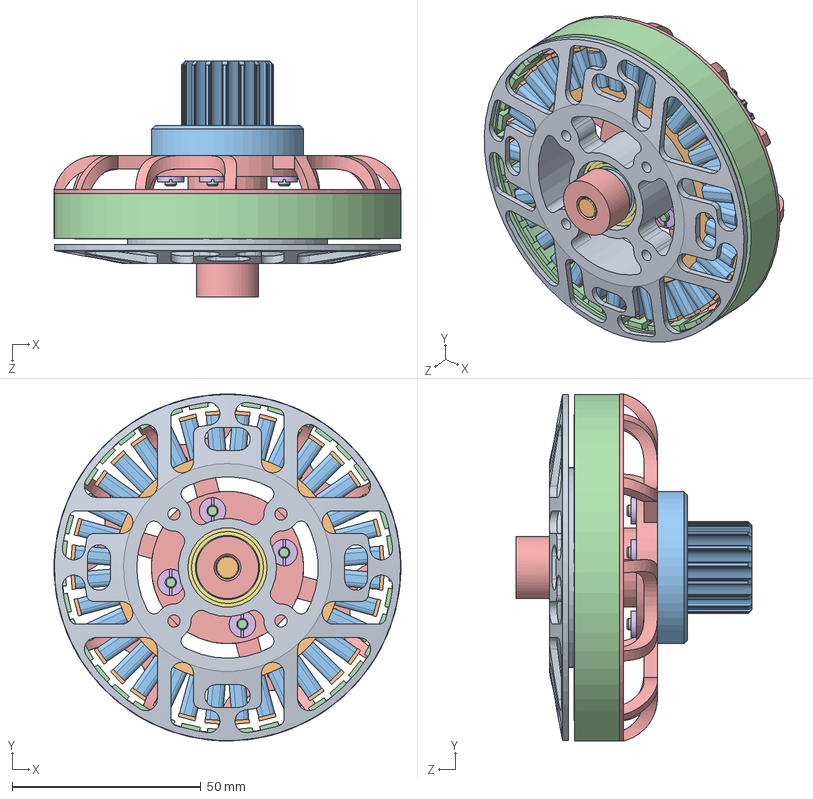
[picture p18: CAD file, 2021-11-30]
solidworks/motor/motor-X83008S.SLDASM
91.8 x 91.8 x 62.4 mm
base^motor-X83008S(2)_motor-X83008S
stator^motor-X83008S(2)_motor-X83008S
coil^motor-X83008S(2)_motor-X83008S x 36
rotor^motor-X83008S(2)_motor-X83008S
outrunner^motor-X83008S(2)_motor-X83008S
screw-mount^motor-X83008S(2)_motor-X83008S x 4
6702ZZ-bearing-15x21x4^motor-X83008S(2)_motor-X83008S x 2
shaft^motor-X83008S(2)_motor-X83008S
Part2^motor-X83008S(2)_motor-X83008S
encoder-magnet-6025
motor-pulley-HTD-5M-16
socket countersunk head screw_am x 4
motor-magnet-mount

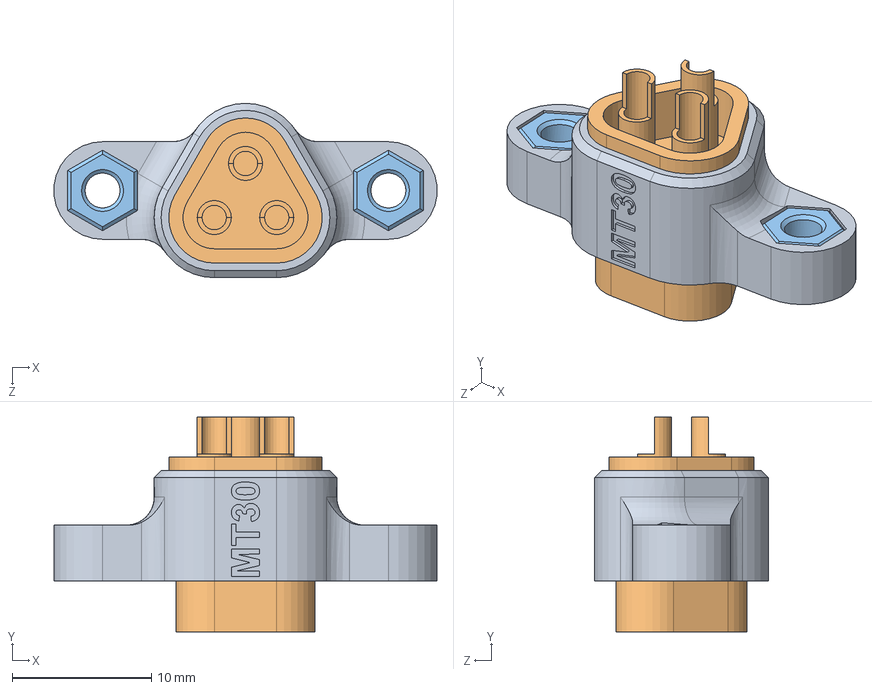
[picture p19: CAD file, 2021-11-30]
solidworks/MT30-M/MT30-with-mount.SLDASM
27.5 x 15.4 x 12.5 mm
MT30-M-mount
MT30-M-female
nut-M2.5 x 2

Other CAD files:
solidworks/multicomp-G373/multicomp-G373.SLDASM
solidworks/odrive/odrive.SLDASM
solidworks/pinheader/pinheader-2.54mm-female-20.SLDASM
solidworks/raspberry-pi-4/rpi-with-cooler.SLDASM
solidworks/50w-resistor/50w-resistor.SLDPRT
solidworks/M12-connector/M12-connector-nut.SLDPRT
solidworks/M12-connector/M12-female-through-panel.SLDPRT
solidworks/M12-connector/M12-male-cable.SLDPRT
solidworks/MT30-M/MT30-M-female.SLDPRT
solidworks/MT30-M/MT30-M-mount.SLDPRT
solidworks/XT60E1-M/XT60E1-M.SLDASM
solidworks/adafruit-feather/adafruit-feather.SLDPRT
solidworks/axle-mount/axle-mount-bottom.SLDPRT
solidworks/axle-mount/axle-mount-top.SLDPRT
solidworks/battery/ninebot-battery-base-mount.SLDPRT
solidworks/battery/ninebot-battery-base.SLDPRT
solidworks/battery/ninebot-battery-connector.SLDPRT
solidworks/battery/ninebot-battery-mount.SLDPRT
solidworks/battery/ninebot-battery-support.SLDPRT
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

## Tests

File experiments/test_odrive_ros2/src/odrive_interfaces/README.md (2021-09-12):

# odrive_interfaces
ROS2 interfaces for ODrive

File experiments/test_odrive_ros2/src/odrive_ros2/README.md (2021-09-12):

# odrive_ros2
ROS2 node for ODrive (Firmware version >= v0.5.1)

## Installation Instructions

### Install ODrive tools
[ODrive Docs](https://docs.odriverobotics.com/)

### Install from source
```bash
# Create workspace
mkdir -p ~/ros2_ws/src
cd ~/ros2_ws/src

# Get node
git clone https://github.com/skymaze/odrive_ros2.git

# Get interface
git clone https://github.com/skymaze/odrive_interfaces.git

# Build
cd ~/ros2_ws
colcon build
```

## Usage Instructions

### Start odrive node
```bash
source ~/ros2_ws/install/local_setup.bash
# To launch with "ros2 run"
ros2 run odrive_ros2 odrive_node
```

### Parameters

- connection.timeout
- battery.max_voltage
- battery.min_voltage
- battery.topic
- joint_state.topic

### Topics

- barrery_percentage
- joint_state

### Services

- connect_odrive
- request_state
- position_cmd
- velocity_cmd

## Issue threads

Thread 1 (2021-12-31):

This looks great! BOM?

samuk, 2021-12-31:
Hi nice work this looks like a good machine. Is there a BOM available anywhere?

grafoteka, 2022-01-27:
Hi @kallaspriit, thank you for sharing the project, it looks great!

I'm with @samuk, is available any BOM of the project? From your video I have identify these components:

- RPlidar S1 ([https://www.slamtec.com/en/Lidar/S1](https://www.slamtec.com/en/Lidar/S1))
- Brushless motor X8308S ([https://es.aliexpress.com/i/32837933318.html](https://es.aliexpress.com/i/32837933318.html))
- IMU BNO-055 ([https://tienda.bricogeek.com/medicion-inercial-imu/802-sensor-inercial-absoluto-9-dof-bno055.html](https://tienda.bricogeek.com/medicion-inercial-imu/802-sensor-inercial-absoluto-9-dof-bno055.html))
- RPI 4B
- Adafruit Feather nRF52840 Sense ([https://learn.adafruit.com/adafruit-feather-sense](https://learn.adafruit.com/adafruit-feather-sense))
- ODrive 3.6 Brushless controller [https://odriverobotics.com/shop/odrive-v36](https://odriverobotics.com/shop/odrive-v36)
- TLE5012B Magnetic Motors Encoders - I could not found with module it is.
- Belt Drive HTD 4.5:1 Gear Ratio
- 32V Battery from Segway Ninebot ES4

kallaspriit, 2022-01-27:
Hey, you've got it right. I've updated the README with link to my own complete BOM. It was not really made for easy replication but rather for myself but maybe it helps :)

Closed 2022-01-27.

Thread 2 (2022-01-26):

Motor Freely Moves when Zero Velocity is Sent

David9696, 2022-01-26:
Hi,

Thanks for sharing this great project.

I tried to implement the sharing package with my own robot. It can be run without issue.

However, when I issued an zero cmd_vel, the wheel would stop but the it is freely to rotate if I rotate it manually. Is this behavior expected? Could I make the wheel not moving or hold when zero cmd_vel is sent? Otherwise the robot would drift for a distance before it really stops.

Hope you could enlighten me.

Thanks.

kallaspriit, 2022-01-27:
Are you using ODrive as well? My robot holds position and the wheels can not be rotated when zero velocity is requested.

kallaspriit, 2022-11-07:
Closing due to inactivity.

Closed 2022-11-07.

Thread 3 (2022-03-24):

problem with  controller manager.

Gilocho, 2022-03-24:
hello I'm having problems running the package with :
`ros2 launch rosbot_bringup robot.launch.py `

stays on the line:
```
[spawner.py-4] [INFO] [1648164601.832733413] [spawner_diff_drive_controller]: Waiting for /controller_manager services
[spawner.py-3] [INFO] [1648164601.833070266] [spawner_joint_state_broadcaster]: Waiting for /controller_manager services
```

and after a few seconds mark:
```
[spawner.py-4] Traceback (most recent call last):
[spawner.py-4]   File "/opt/ros/foxy/lib/controller_manager/spawner.py", line 204, in <module>
[spawner.py-4]     sys.exit(main())
[spawner.py-4]   File "/opt/ros/foxy/lib/controller_manager/spawner.py", line 123, in main
[spawner.py-4]     if is_controller_loaded(node, controller_manager_name, controller_name):
[spawner.py-4]   File "/opt/ros/foxy/lib/controller_manager/spawner.py", line 65, in is_controller_loaded
[spawner.py-4]     controllers = list_controllers(node, controller_manager).controller
[spawner.py-4]   File "/opt/ros/foxy/lib/python3.8/site-packages/controller_manager/controller_manager_services.py", line 49, in list_controllers
[spawner.py-4]     return service_caller(node, f'{controller_manager_name}/list_controllers',
[spawner.py-4]   File "/opt/ros/foxy/lib/python3.8/site-packages/controller_manager/controller_manager_services.py", line 29, in service_caller
[spawner.py-4]     raise RuntimeError(f'Could not contact service {service_name}')
[spawner.py-4] RuntimeError: Could not contact service /controller_manager/list_controllers
[spawner.py-3] Traceback (most recent call last):
[spawner.py-3]   File "/opt/ros/foxy/lib/controller_manager/spawner.py", line 204, in <module>
[spawner.py-3]     sys.exit(main())
[spawner.py-3]   File "/opt/ros/foxy/lib/controller_manager/spawner.py", line 123, in main
[spawner.py-3]     if is_controller_loaded(node, controller_manager_name, controller_name):
[spawner.py-3]   File "/opt/ros/foxy/lib/controller_manager/spawner.py", line 65, in is_controller_loaded
[spawner.py-3]     controllers = list_controllers(node, controller_manager).controller
[spawner.py-3]   File "/opt/ros/foxy/lib/python3.8/site-packages/controller_manager/controller_manager_services.py", line 49, in list_controllers
[spawner.py-3]     return service_caller(node, f'{controller_manager_name}/list_controllers',
[spawner.py-3]   File "/opt/ros/foxy/lib/python3.8/site-packages/controller_manager/controller_manager_services.py", line 29, in service_caller
[spawner.py-3]     raise RuntimeError(f'Could not contact service {service_name}')
[spawner.py-3] RuntimeError: Could not contact service /controller_manager/list_controllers
[ERROR] [spawner.py-4]: process has died [pid 15312, exit code 1, cmd '/opt/ros/foxy/lib/controller_manager/spawner.py diff_drive_controller --ros-args'].
[ERROR] [spawner.py-3]: process has died [pid 15310, exit code 1, cmd '/opt/ros/foxy/lib/controller_manager/spawner.py joint_state_broadcaster --ros-args'].
```
directly use the library: https://github.com/Factor-Robotics/odrive_ros2_control/
and let me control the two motors without problems
any idea why this could happen?

thanks for you help

kallaspriit, 2022-11-07:
Sorry but don't know how to help you with this one. Sometimes ROS fails for no apparent reason and just restarting everything makes it work again.

Closed 2022-11-07.

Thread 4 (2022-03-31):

rplidar data frame

HusamZain, 2022-03-31:
Great work, and thank you for sharing !
I'm building the same project and using almost the same hardware you have , but I'm facing a problem with the Laserscan data that published from the rplidar package that you used ,  it's rotates with the robot when I rotate the robot, so I was wondering if you countered the same issue when you worked with rplidar?
as you can see in the pic, the laserscan data rotates when I rotate the robot, not sure is it beacouse the TF, but I have a similar urdf file as yours(odom>>base_link and base_link>>lidar_link)

kallaspriit, 2022-07-10:
Haven't had problems with the library, check your transforms :)

Closed 2022-07-10.

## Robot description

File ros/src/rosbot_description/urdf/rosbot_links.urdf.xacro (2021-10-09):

<?xml version="1.0"?>
<robot xmlns:xacro="http://www.ros.org/wiki/xacro">

  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
  <xacro:include filename="$(find rosbot_description)/urdf/inertia.urdf.xacro" />

  <xacro:macro name="rosbot_links" params="prefix">

    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
    <xacro:property name="body_mass" value="6.0" />
    <xacro:property name="body_width" value="0.46" />
    <xacro:property name="body_length" value="0.3" />
    <xacro:property name="body_height" value="0.17" />
    <xacro:property name="body_ground_offset" value="0.0575" />

    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
    <xacro:property name="lidar_height" value="0.055" />
    <xacro:property name="lidar_radius" value="0.0275" />

    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
    <xacro:property name="rear_wheel_mass" value="0.5" />
    <xacro:property name="rear_wheel_width" value="0.05" />
    <xacro:property name="rear_wheel_radius" value="0.0975" />
    <xacro:property name="rear_wheel_origin_x" value="-0.1" />
    <xacro:property name="rear_wheel_distance" value="0.241" />

    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
    <xacro:property name="front_wheel_mass" value="0.2" />
    <xacro:property name="front_wheel_width" value="0.025" />
    <xacro:property name="front_wheel_radius" value="0.0385" />
    <xacro:property name="front_wheel_origin_x" value="0.26757" />

    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
    <xacro:property name="imu_size" value="0.02" />

    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
    <xacro:property name="camera_width" value="0.025" />
    <xacro:property name="camera_length" value="0.05" />
    <xacro:property name="camera_height" value="0.025" />

    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
    <link name="${prefix}base_link"/>

    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
    <link name="base_footprint"/>
    <joint name="${prefix}base_joint" type="fixed">
      <parent link="${prefix}base_link"/>
      <child link="${prefix}base_footprint" />
      <origin xyz="${rear_wheel_origin_x * -1} 0 0" rpy="0 0 0"/>
    </joint>

    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
    <link name="${prefix}body">
      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
      <xacro:box_inertia m="${body_mass}" w="${body_width}" d="${body_length}" h="${body_height}"/>
    </link>
    <joint name="${prefix}body_joint" type="fixed">
      <parent link="${prefix}base_link"/>
      <child link="${prefix}body"/>
      <origin xyz="${-rear_wheel_origin_x} 0 ${body_ground_offset + body_height / 2}" rpy="0 0 0"/>
      <axis xyz="0 0 1"/>
    </joint>

    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
    <link name="${prefix}left_wheel">
      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
      <xacro:cylinder_inertia m="${rear_wheel_mass}" r="${rear_wheel_radius}" h="${rear_wheel_width}"/>
    </link>
    <joint name="${prefix}left_wheel_joint" type="continuous">
      <parent link="${prefix}base_link"/>
      <child link="${prefix}left_wheel"/>
      <origin xyz="0 ${rear_wheel_distance/2} ${rear_wheel_radius}" rpy="0 0 0"/>
      <axis xyz="0 1 0"/>
      <dynamics damping="0.2"/>
    </joint>

    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
    <link name="${prefix}right_wheel">
      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
      <xacro:cylinder_inertia m="${rear_wheel_mass}" r="${rear_wheel_radius}" h="${rear_wheel_width}"/>
    </link>
    <joint name="${prefix}right_wheel_joint" type="continuous">
      <parent link="${prefix}base_link"/>
      <child link="${prefix}right_wheel"/>
      <origin xyz="0 -${rear_wheel_distance/2} ${rear_wheel_radius}" rpy="0 0 0"/>
      <axis xyz="0 1 0"/>
      <dynamics damping="0.2"/>
    </joint>

    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
    <link name="${prefix}front_wheel">
      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
      <xacro:sphere_inertia m="${front_wheel_mass}" r="${front_wheel_radius}"/>
    </link>
    <joint name="${prefix}front_wheel_joint" type="fixed">
      <parent link="${prefix}body"/>
      <child link="${prefix}front_wheel"/>
      <origin xyz="${front_wheel_origin_x} 0 ${front_wheel_radius - body_height / 2 - body_ground_offset}" rpy="0 0 0"/>
      <axis xyz="0 0 1"/>
      <dynamics damping="0.2"/>
    </joint>

    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
    <link name="${prefix}base_laser">
      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
    </link>
    <joint name="${prefix}lidar_joint" type="fixed">
      <parent link="${prefix}body"/>
      <child link="${prefix}base_laser"/>
      <origin xyz="0 0 ${body_height / 2 + lidar_height / 2}" rpy="0 0 ${pi}"/>
      <axis xyz="0 0 1"/>
    </joint>

    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
    <link name="imu_link">
      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
      <xacro:cylinder_inertia m="0.01" r="${imu_size}" h="${imu_size}"/>
    </link>
    <joint name="imu_joint" type="fixed">
      <parent link="body"/>
      <child link="imu_link"/>
      <origin xyz="${rear_wheel_origin_x} 0 ${body_height / 2 + imu_size / 2}" rpy="0 0 0"/>
      <axis xyz="0 0 1"/>
    </joint>

    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
    <link name="${prefix}rgb_camera_link">
      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
    </link>
    <joint name="${prefix}camera_joint" type="fixed">
      <parent link="${prefix}body"/>
      <child link="${prefix}rgb_camera_link"/>
      <origin xyz="${body_width / 2} 0 ${body_height / 2 + camera_height / 2}" rpy="0 0 0"/>
    </joint>

    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
    <link name="depth_camera_link"/>
    <joint name="depth_camera_joint" type="fixed">
      <origin xyz="0 0 0" rpy="${-pi/2} 0 ${pi/2}"/>
      <parent link="rgb_camera_link"/>
      <child link="depth_camera_link"/>
    </joint>

  </xacro:macro>

</robot>

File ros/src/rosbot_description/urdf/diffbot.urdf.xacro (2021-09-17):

<?xml version="1.0"?>
<robot xmlns:xacro="http://www.ros.org/wiki/xacro">

  <xacro:macro name="diffbot" params="prefix">

  <!-- Constants for robot dimensions -->
  <xacro:property name="PI" value="3.1415926535897931"/>
  <xacro:property name="base_mass" value="0.3" /> <!-- arbitrary value for base mass -->
  <xacro:property name="base_width" value="0.1" />
  <xacro:property name="base_length" value="0.1" />
  <xacro:property name="base_height" value="0.05" />
  <xacro:property name="wheel_mass" value="0.3" /> <!-- arbitrary value for wheel mass -->
  <xacro:property name="wheel_len" value="0.020" />
  <xacro:property name="wheel_radius" value="0.015" />
  <xacro:property name="caster_wheel_mass" value="0.1" /> <!-- arbitrary value for caster wheel mass -->
  <xacro:property name="caster_wheel_radius" value="0.015" />
  <xacro:property name="z_offset" value="-${base_height/2}" /> <!-- Space btw top of beam and the each joint -->

  <!-- Base Link -->
  <link name="${prefix}base_link">
    <collision>
      <origin xyz="0 0 0" rpy="0 0 0"/>
      <geometry>
        <box size="${base_width} ${base_length} ${base_height}"/>
      </geometry>
    </collision>

    <visual>
      <origin xyz="0 0 0" rpy="0 0 0"/>
      <geometry>
        <box size="${base_width} ${base_length} ${base_height}"/>
      </geometry>
      <material name="orange"/>
    </visual>

    <inertial>
      <origin xyz="0 0 0" rpy="0 0 0"/>
      <mass value="${base_mass}"/>
      <inertia ixx="${base_mass / 12.0 * (base_length*base_length + base_height*base_height)}" ixy="0.0" ixz="0.0" iyy="${base_mass / 12.0 * (base_height*base_height + base_width*base_width)}" iyz="0.0" izz="${base_mass / 12.0 * (base_width*base_width + base_length*base_length)}"/>
      </inertial>
    </link>

    <joint name="${prefix}left_wheel_joint" type="continuous">
      <parent link="${prefix}base_link"/>
      <child link="${prefix}left_wheel"/>
      <origin xyz="0 -${base_width/2} ${z_offset}" rpy="0 0 0"/>
      <axis xyz="0 1 0"/>
      <dynamics damping="0.2"/>
    </joint>

    <!-- left wheel Link -->
    <link name="${prefix}left_wheel">
      <collision>
        <origin xyz="0 0 0" rpy="${PI/2} 0 0"/>
        <geometry>
          <cylinder length="${wheel_len}" radius="${wheel_radius}"/>
        </geometry>
      </collision>

      <visual>
        <origin xyz="0 0 0" rpy="${PI/2} 0 0"/>
        <geometry>
          <cylinder length="${wheel_len}" radius="${wheel_radius}"/>
        </geometry>
        <material name="black"/>
      </visual>

      <inertial>
        <origin xyz="0 0 0" rpy="${PI/2} 0 0"/>
        <mass value="${wheel_mass}"/>
        <inertia ixx="${wheel_mass / 12.0 * (3*wheel_radius + wheel_len*wheel_len)}" ixy="0.0" ixz="0.0" iyy="${wheel_mass / 12.0 * wheel_radius*wheel_radius}" iyz="0.0" izz="${wheel_mass / 12.0 * wheel_radius*wheel_radius}"/>
        </inertial>
      </link>

    <joint name="${prefix}right_wheel_joint" type="continuous">
      <parent link="${prefix}base_link"/>
      <child link="${prefix}right_wheel"/>
      <origin xyz="0 ${base_width/2} ${z_offset}" rpy="0 0 0"/>
      <axis xyz="0 1 0"/>
      <dynamics damping="0.2"/>
    </joint>

    <!-- right wheel Link -->
    <link name="${prefix}right_wheel">
      <collision>
        <origin xyz="0 0 0" rpy="${PI/2} 0 0"/>
        <geometry>
          <cylinder length="${wheel_len}" radius="${wheel_radius}"/>
        </geometry>
      </collision>

      <visual>
        <origin xyz="0 0 0" rpy="${PI/2} 0 0"/>
        <geometry>
          <cylinder length="${wheel_len}" radius="${wheel_radius}"/>
        </geometry>
        <material name="black"/>
      </visual>

      <inertial>
        <origin xyz="0 0 0" rpy="${PI/2} 0 0"/>
        <mass value="${wheel_mass}"/>
        <inertia ixx="${wheel_mass / 12.0 * (3*wheel_radius + wheel_len*wheel_len)}" ixy="0.0" ixz="0.0" iyy="${wheel_mass / 12.0 * wheel_radius*wheel_radius}" iyz="0.0" izz="${wheel_mass / 12.0 * wheel_radius*wheel_radius}"/>
        </inertial>
      </link>

    <joint name="${prefix}caster_frontal_wheel_joint" type="fixed">
      <parent link="${prefix}base_link"/>
      <child link="${prefix}caster_frontal_wheel"/>
      <origin xyz="${base_width/2 - caster_wheel_radius} 0 ${z_offset}" rpy="0 0 0"/>
    </joint>

    <!-- caster frontal wheel Link -->
    <link name="${prefix}caster_frontal_wheel">
      <collision>
        <origin xyz="0 0 0" rpy="0 0 0"/>
        <geometry>
          <sphere radius="${caster_wheel_radius}"/>
        </geometry>
      </collision>

      <visual>
        <origin xyz="0 0 0" rpy="0 0 0"/>
        <geometry>
          <sphere radius="${caster_wheel_radius}"/>
        </geometry>
        <material name="white"/>
      </visual>

      <inertial>
        <origin xyz="0 0 0" rpy="0 0 0"/>
        <mass value="${caster_wheel_mass}"/>
        <inertia ixx="${caster_wheel_mass * 0.4 * (caster_wheel_radius * caster_wheel_radius)}" ixy="0.0" ixz="0.0" iyy="${caster_wheel_mass * 0.4 * (caster_wheel_radius * caster_wheel_radius)}" iyz="0.0" izz="${caster_wheel_mass * 0.4 * (caster_wheel_radius * caster_wheel_radius)}"/>
        </inertial>
      </link>

    <joint name="${prefix}caster_rear_wheel_joint" type="fixed">
      <parent link="${prefix}base_link"/>
      <child link="${prefix}caster_rear_wheel"/>
      <origin xyz="${-base_width/2 + caster_wheel_radius} 0 ${z_offset}" rpy="0 0 0"/>
    </joint>

    <!-- caster rear wheel Link -->
    <link name="${prefix}caster_rear_wheel">
      <collision>
        <origin xyz="0 0 0" rpy="0 0 0"/>
        <geometry>
          <sphere radius="${caster_wheel_radius}"/>
        </geometry>
      </collision>

      <visual>
        <origin xyz="0 0 0" rpy="0 0 0"/>
        <geometry>
          <sphere radius="${caster_wheel_radius}"/>
        </geometry>
        <material name="white"/>
      </visual>

      <inertial>
        <origin xyz="0 0 0" rpy="0 0 0"/>
        <mass value="${caster_wheel_mass}"/>
        <inertia ixx="${caster_wheel_mass * 0.4 * (caster_wheel_radius * caster_wheel_radius)}" ixy="0.0" ixz="0.0" iyy="${caster_wheel_mass * 0.4 * (caster_wheel_radius * caster_wheel_radius)}" iyz="0.0" izz="${caster_wheel_mass * 0.4 * (caster_wheel_radius * caster_wheel_radius)}"/>
        </inertial>
      </link>

  </xacro:macro>

</robot>

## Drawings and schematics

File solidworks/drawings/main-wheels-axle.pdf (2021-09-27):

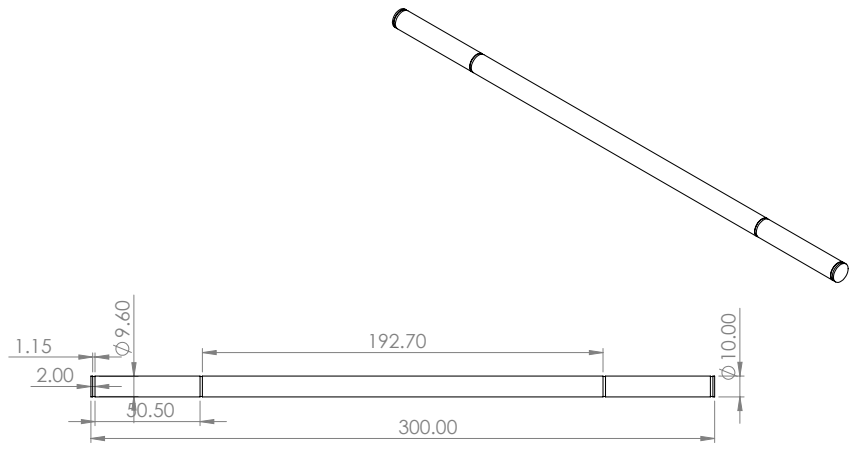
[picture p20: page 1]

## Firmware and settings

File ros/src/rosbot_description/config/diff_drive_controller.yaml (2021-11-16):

controller_manager:
  ros__parameters:
    update_rate: 100 # Hz

    joint_state_broadcaster:
      type: joint_state_broadcaster/JointStateBroadcaster

    diff_drive_controller:
      type: diff_drive_controller/DiffDriveController

diff_drive_controller:
  ros__parameters:
    left_wheel_names: ["left_wheel_joint"]
    right_wheel_names: ["right_wheel_joint"]
    # write_op_modes: ["motor_controller"]

    # TODO: set correct robot parameters
    wheel_separation: 0.241
    #wheels_per_side: 1  # actually 2, but both are controlled by 1 signal
    wheel_radius: 0.0975

    wheel_separation_multiplier: 1.0
    # left_wheel_radius_multiplier: 1.0
    # right_wheel_radius_multiplier: 1.0
    # wheels have gearbox ratio of 4.5 (inverse 0.222222222)
    left_wheel_radius_multiplier: 0.222222222
    right_wheel_radius_multiplier: 0.222222222

    publish_rate: 50.0
    odom_frame_id: odom
    base_frame_id: base_link

    # error model
    # values provided in the example, not sure how to calculate
    # https://manialabs.wordpress.com/2012/08/06/covariance-matrices-with-a-practical-example/
    # pose_covariance_diagonal: [0.001, 0.001, 0.001, 0.001, 0.001, 0.01]
    # twist_covariance_diagonal: [0.001, 0.001, 0.001, 0.001, 0.001, 0.01]
    # pose_covariance_diagonal: [0.0, 0.0, 0.0, 0.0, 0.0, 0.0]
    # twist_covariance_diagonal: [0.0, 0.0, 0.0, 0.0, 0.0, 0.0]
    pose_covariance_diagonal:
      [0.001, 0.001, 1000000.0, 1000000.0, 1000000.0, 1000.0]
    twist_covariance_diagonal:
      [0.001, 0.001, 1000000.0, 1000000.0, 1000000.0, 1000.0]

    # open_loop: true
    open_loop: false
    enable_odom_tf: true

    cmd_vel_timeout: 0.5

    # publish_limited_velocity: true

    # unstamped velocity uses /diff_drive_controller/cmd_vel_unstamped
    use_stamped_vel: false

    # stamped velocity uses /diff_drive_controller/cmd_vel
    # use_stamped_vel: true

    velocity_rolling_window_size: 10

    # preserve turning radius when limiting speed/acceleration/jerk
    preserve_turning_radius: true

    # publish limited velocity
    publish_cmd: true

    # publish wheel data
    publish_wheel_data: true

    # velocity and acceleration limits
    # whenever a min_* is unspecified, default to -max_*
    linear.x.has_velocity_limits: true
    linear.x.has_acceleration_limits: true
    linear.x.has_jerk_limits: false
    linear.x.max_velocity: 2.0
    linear.x.min_velocity: -2.0
    linear.x.min_acceleration: -3.0
    linear.x.max_acceleration: 3.0
    linear.x.max_jerk: 0.0
    linear.x.min_jerk: 0.0

    angular.z.has_velocity_limits: true
    angular.z.has_acceleration_limits: true
    angular.z.has_jerk_limits: false
    angular.z.max_velocity: 6.28
    angular.z.min_velocity: -6.28
    angular.z.max_acceleration: 25.0
    angular.z.min_acceleration: -25.0
    angular.z.max_jerk: 0.0
    angular.z.min_jerk: 0.0

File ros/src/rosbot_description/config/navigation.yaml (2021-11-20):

bt_navigator:
  ros__parameters:
    global_frame: map
    robot_base_frame: base_link
    # odom_topic: /odometry/filtered
    odom_topic: /odom
    enable_groot_monitoring: True
    groot_zmq_publisher_port: 1666
    groot_zmq_server_port: 1667
    default_bt_xml_filename: "src/rosbot_description/config/navigate_w_replanning_and_recovery.xml"
    plugin_lib_names:
      - nav2_compute_path_to_pose_action_bt_node
      - nav2_follow_path_action_bt_node
      - nav2_back_up_action_bt_node
      - nav2_spin_action_bt_node
      - nav2_wait_action_bt_node
      - nav2_clear_costmap_service_bt_node
      - nav2_is_stuck_condition_bt_node
      - nav2_goal_reached_condition_bt_node
      - nav2_goal_updated_condition_bt_node
      - nav2_initial_pose_received_condition_bt_node
      - nav2_reinitialize_global_localization_service_bt_node
      - nav2_rate_controller_bt_node
      - nav2_distance_controller_bt_node
      - nav2_speed_controller_bt_node
      - nav2_truncate_path_action_bt_node
      - nav2_goal_updater_node_bt_node
      - nav2_recovery_node_bt_node
      - nav2_pipeline_sequence_bt_node
      - nav2_round_robin_node_bt_node
      - nav2_transform_available_condition_bt_node
      - nav2_time_expired_condition_bt_node
      - nav2_distance_traveled_condition_bt_node

controller_server:
  ros__parameters:
    controller_frequency: 20.0
    min_x_velocity_threshold: 0.001
    # we are not expecting sideways speed
    min_y_velocity_threshold: 0.5
    min_theta_velocity_threshold: 0.001
    # failure_tolerance: 0
    # failure_tolerance: 5
    progress_checker_plugin: "progress_checker"
    goal_checker_plugin: "goal_checker"
    controller_plugins: ["FollowPath"]

    # Progress checker parameters
    progress_checker:
      plugin: "nav2_controller::SimpleProgressChecker"
      required_movement_radius: 0.25
      movement_time_allowance: 10.0

    # Goal checker parameters
    goal_checker:
      plugin: "nav2_controller::SimpleGoalChecker"
      # xy_goal_tolerance: 0.25
      # yaw_goal_tolerance: 0.5
      # xy_goal_tolerance: 0.2
      xy_goal_tolerance: 0.25
      yaw_goal_tolerance: 0.1
      stateful: True

    # DWB parameters
    FollowPath:
      plugin: "dwb_core::DWBLocalPlanner"
      debug_trajectory_details: True
      min_vel_x: -0.5
      max_vel_x: 0.5
      min_vel_y: 0.0
      max_vel_y: 0.0
      max_vel_theta: 0.5
      min_speed_xy: -0.5
      max_speed_xy: 0.5
      min_speed_theta: 0.0
      acc_lim_x: 0.05
      decel_lim_x: -0.05
      acc_lim_y: 0.0
      decel_lim_y: 0.0
      acc_lim_theta: 3.14
      decel_lim_theta: -3.14
      vx_samples: 20
      vy_samples: 5
      vtheta_samples: 20
      sim_time: 1.7
      linear_granularity: 0.05
      angular_granularity: 0.025
      transform_tolerance: 0.2
      xy_goal_tolerance: 0.1
      trans_stopped_velocity: 0.25
      short_circuit_trajectory_evaluation: True
      stateful: True
      critics:
        [
          "RotateToGoal",
          "Oscillation",
          "BaseObstacle",
          "GoalAlign",
          "PathAlign",
          "PathDist",
          "GoalDist",
        ]
      # BaseObstacle:
      #   scale: 0.02
      # PathAlign:
      #   scale: 32.0
      # PathAlign:
      #   forward_point_distance: 0.1
      # GoalAlign:
      #   scale: 24.0
      # GoalAlign:
      #   forward_point_distance: 0.1
      # PathDist:
      #   scale: 32.0
      # GoalDist:
      #   scale: 24.0
      # RotateToGoal:
      #   scale: 32.0
      #   slowing_factor: 5.0
      #   lookahead_time: -1.0

# local_costmap:
#   local_costmap:
#     ros__parameters:
#       update_frequency: 5.0
#       publish_frequency: 2.0
#       global_frame: odom
#       robot_base_frame: base_link
#       rolling_window: true
#       width: 3
#       height: 3
#       resolution: 0.05
#       footprint: "[ [0.3, 0.2], [0.3, -0.2], [-0.1, -0.2], [-0.1, 0.2] ]"
#       plugins: ["inflation_layer"]
#       inflation_layer:
#         plugin: "nav2_costmap_2d::InflationLayer"
#         inflation_radius: 0.55
#         cost_scaling_factor: 3.0
#       always_send_full_costmap: True
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

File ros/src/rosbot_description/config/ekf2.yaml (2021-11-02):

### ekf config file ###
ekf_filter_node:
    ros__parameters:

        use_sim_time: true

        
# The frequency, in Hz, at which the filter will output a position estimate. Note that the filter will not begin
# computation until it receives at least one message from one of the inputs. It will then run continuously at the
# frequency specified here, regardless of whether it receives more measurements. Defaults to 30 if unspecified.
        frequency: 30.0

# The period, in seconds, after which we consider a sensor to have timed out. In this event, we carry out a predict
# cycle on the EKF without correcting it. This parameter can be thought of as the minimum frequency with which the
# filter will generate new output. Defaults to 1 / frequency if not specified.
        sensor_timeout: 0.1

# ekf_localization_node and ukf_localization_node both use a 3D omnidirectional motion model. If this parameter is
# set to true, no 3D information will be used in your state estimate. Use this if you are operating in a planar
# environment and want to ignore the effect of small variations in the ground plane that might otherwise be detected
# by, for example, an IMU. Defaults to false if unspecified.
        two_d_mode: true

# Use this parameter to provide an offset to the transform generated by ekf_localization_node. This can be used for
# future dating the transform, which is required for interaction with some other packages. Defaults to 0.0 if
# unspecified.
        transform_time_offset: 0.0

# Use this parameter to provide specify how long the tf listener should wait for a transform to become available. 
# Defaults to 0.0 if unspecified.
        transform_timeout: 0.0

# If you're having trouble, try setting this to true, and then echo the /diagnostics_agg topic to see if the node is
# unhappy with any settings or data.
        print_diagnostics: true

# Debug settings. Not for the faint of heart. Outputs a ludicrous amount of information to the file specified by
# debug_out_file. I hope you like matrices! Please note that setting this to true will have strongly deleterious
# effects on the performance of the node. Defaults to false if unspecified.
        debug: false

# Defaults to "robot_localization_debug.txt" if unspecified. Please specify the full path.
        debug_out_file: /path/to/debug/file.txt

# Whether to broadcast the transformation over the /tf topic. Defaults to true if unspecified.
        publish_tf: true

# Whether to publish the acceleration state. Defaults to false if unspecified.
        publish_acceleration: false

# If the filter sees a jump back in time, the filter is reset (convenient for testing with rosbags!)
        reset_on_time_jump: true

# REP-105 (http://www.ros.org/reps/rep-0105.html) specifies four principal coordinate frames: base_link, odom, map, and
# earth. base_link is the coordinate frame that is affixed to the robot. Both odom and map are world-fixed frames.
# The robot's position in the odom frame will drift over time, but is accurate in the short term and should be
# continuous. The odom frame is therefore the best frame for executing local motion plans. The map frame, like the odom
# frame, is a world-fixed coordinate frame, and while it contains the most globally accurate position estimate for your
# robot, it is subject to discrete jumps, e.g., due to the fusion of GPS data or a correction from a map-based
# localization node. The earth frame is used to relate multiple map frames by giving them a common reference frame.
# ekf_localization_node and ukf_localization_node are not concerned with the earth frame.
# Here is how to use the following settings:
# 1. Set the map_frame, odom_frame, and base_link frames to the appropriate frame names for your system.
#     1a. If your system does not have a map_frame, just remove it, and make sure "world_frame" is set to the value of
#         odom_frame.
# 2. If you are fusing continuous position data such as wheel encoder odometry, visual odometry, or IMU data, set
#   "world_frame" to your odom_frame value. This is the default behavior for robot_localization's state estimation nodes.
# 3. If you are fusing global absolute position data that is subject to discrete jumps (e.g., GPS or position updates
# from landmark observations) then:
#     3a. Set your "world_frame" to your map_frame value
#     3b. MAKE SURE something else is generating the odom->base_link transform. Note that this can even be another state
#         estimation node from robot_localization! However, that instance should *not* fuse the global data.
        map_frame: map                   # Defaults to "map" if unspecified
        odom_frame: odom                 # Defaults to "odom" if unspecified
        base_link_frame: base_footprint  # Defaults to "base_link" if unspecified
        world_frame: odom                # Defaults to the value of odom_frame if unspecified
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

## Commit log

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2021-06-24 Modelled 30x30 profile and main wheels axle
    [main-wheels-axle.SLDPRT, profile-30x30.SLDPRT, profile-30x30.dxf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]
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2021-06-24 Improved axle mount, added print
    [axle-mount-bottom-v1.STL, axle-mount-bottom.SLDPRT, axle-mount-top-v1.STL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]
2021-06-28 Added second frame rail
    [axle-mount.SLDASM, robot.SLDASM, wheel.SLDASM]
2021-06-28 Added battery, enclosure, frame profiles
    [axle-mount.SLDASM, multicomp-g373.SLDPRT, ninebot-battery.SLDPRT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]
2021-06-28 Modelled timing belt, added motor
    [HTD-5M-460.SLDPRT, axle-mount.SLDASM, motor-X83008S.SLDASM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]
2021-06-29 Added shorter belt, rearranged enclosure and battery
    [HTD-5M-425.SLDPRT, HTD-5M-460.SLDPRT, axle-mount.SLDASM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]
2021-06-29 Created motor pulley profile, mounting
    [axle-mount.SLDASM, motor-X83008S.SLDASM, motor-pulley-HTD-5M-16-v1.STL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]
2021-06-29 Modelled encoder magnet and magnet mount
    [axle-mount.SLDASM, encoder-magnet-6025.SLDPRT, encoder-magnet-mount.SLDPRT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]
2021-06-29 Added encoder mount print, started with encoder board
    [axle-mount-bottom-v1.STL, encoder-TLE5012B.SLDPRT, encoder-magnet-mount-v1.STL]
2021-06-30 Working on motor mount
    [axle-mount.SLDASM, encoder-TLE5012B.SLDPRT, motor-X83008S.SLDASM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]
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2021-06-30 Working on motor mount, organized main assembly parts
    [axle-mount.SLDASM, motor-X83008S.SLDASM, motor-encoder-mount.SLDPRT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]
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2021-07-05 Working on motor mounts
    [Mirrormotor-frame-mount.SLDPRT, axle-mount.SLDASM, motor-X83008S.SLDASM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]
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2021-07-05 Working on motor mount mounting
    [Mirrormotor-frame-mount.SLDPRT, axle-mount.SLDASM, bolt-socket-M6-25mm.SLDPRT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]
2021-07-06 Added motor frame mount spacer
    [Mirrormotor-frame-mount.SLDPRT, axle-mount.SLDASM, motor-X83008S.SLDASM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]
2021-07-06 Added motor frame mount bridge, improved mount
    [Mirrormotor-frame-mount.SLDPRT, axle-mount.SLDASM, motor-X83008S.SLDASM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]
2021-07-06 Improved motor mounting, bridge
    [Mirrormotor-frame-mount.SLDPRT, axle-mount.SLDASM, bolt-countersunk-M3-16mm.SLDPRT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]
2021-07-28 Working on battery connector
    [axle-mount.SLDASM, motor-X83008S.SLDASM, motor-frame-mount-left-v1.STL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]
2021-07-29 Working on battery mount
    [axle-mount.SLDASM, motor-X83008S.SLDASM, ninebot-battery-connector-v3.STL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]
2021-07-29 Added battery mount rear base
    [axle-mount.SLDASM, motor-X83008S.SLDASM, ninebot-battery-base.SLDPRT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]
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2021-08-02 Modelled multicomp G373 enclosure
    [XT60E1-M.SLDASM, axle-mount.SLDASM, encoder-magnet-mount v1.STL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]
2021-08-02 Added odrive, started with electronics box
    [electronics-box-odrive.SLDDRW, electronics-box.SLDASM, multicomp-G373-bottom.SLDPRT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]
2021-08-02 Added odrive 50W resistor
    [50w-resistor.SLDPRT, electronics-box-odrive.SLDDRW, electronics-box-resistor.SLDDRW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]
2021-08-02 Added variable voltage regulator, electronics box to robot
    [axle-mount.SLDASM, electronics-box-resistor.SLDDRW, electronics-box.SLDASM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]
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2021-08-03 Improved mounting hardware, added electronics box holes
    [axle-mount.SLDASM, corner-mount.SLDPRT, electronics-box.SLDASM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]
2021-08-03 Modelled M12 connectors, added XT60 through panel mount
    [M12-connector-nut.SLDPRT, M12-female-through-panel.SLDPRT, M12-male-cable.SLDPRT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]
2021-08-04 Modelled MT30 female connector and 3D printed mount for it
    [MT30-M-female.SLDPRT, MT30-M-mount v1.STL, MT30-M-mount v2.STL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]
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2021-08-04 Added raspberry pi and modelled cooler for it
    [1.0 Plate raspberry Pi 4.SLDPRT, 1.1 part 1 metal pin.SLDPRT, 10.0 Female USB connector.SLDPRT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]
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2021-08-05 Added adafruit feather, proto pcb to electronics box
    [MT30-with-mount.SLDASM, XT60E1-M.SLDASM, adafruit-feather.SLDPRT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]
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2021-08-17 Modelled in front of the robot wheel mount
    [MT30-with-mount.SLDASM, XT60E1-M.SLDASM, axle-mount.SLDASM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]
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2021-08-21 Added front wheel mount cap, nut adapter, improved front mount
    [MT30-with-mount.SLDASM, Mirrorbearing-10x5x4.SLDPRT, Mirrorfront-caster-bottom.SLDPRT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]
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2021-09-03 Improved front wheel mount to accept office chair caster wheel
    [MT30-with-mount.SLDASM, Mirrorfront-wheel-mount.SLDPRT, Mirrorfront-wheel-rim.SLDPRT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]
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2021-09-17 Renamed joint0, joint1 to left and right wheel joints
    [odrive.ros2_control.xacro, odrive.urdf.xacro, odrive_controllers.yaml]
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2021-09-19 Fixed urdf issue
    [UNUSED_rosbot.ros2_control.xacro, rosbot_system.ros2_control.xacro]
2021-09-19 Fixed xacro todos
    [rosbot.urdf.xacro, rosbot_system.ros2_control.xacro]
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2021-09-20 Added rviz and teleop launch scripts, removed caster wheels
    [rosbot.urdf.xacro]
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2021-09-20 Replaced wheel offset with body offset
    [rosbot.urdf.xacro]
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2021-09-20 Fixed acceleration setting
    [rosbot_controllers.yaml]
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2021-09-28 Added optional teleop to main rosbot launch file
    [rosbot_controllers.yaml]
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2021-09-28 Changed lidar joint to fixed
    [rosbot.urdf.xacro]
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2021-09-28 Fixed lidar joint origin rotation
    [rosbot.urdf.xacro]
2021-09-29 Improved robot description, added test body mesh, made lidar cylinder
    [rosbot.materials.xacro, rosbot.urdf.xacro]
2021-09-29 Fixed xml todo
    [rosbot.urdf.xacro]
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2021-10-07 Moved rosbot controller config, added gazebo diff drive
    [rosbot.gazebo.xacro, rosbot_controllers.yaml]
2021-10-07 Added ekf and nav2_params configs, renamed rosbot links
    [rosbot_links.urdf.xacro, rosbot_system.urdf.xacro]
2021-10-07 Renamed rosbot system file, removed rosbot system name
    [rosbot.urdf.xacro]
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2021-10-07 Fixed typo
    [rosbot_links.urdf.xacro]
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2021-10-09 Added test office world, simulation now uses gpu laser
    [my_world.sdf, office.sdf, rosbot.gazebo.xacro]
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2021-10-09 Improved camera simulation, fixed z-fighting
    [office.sdf, rosbot.gazebo.xacro]
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2021-11-10 Fixed imu config path
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2021-11-10 Reverted to older bno055
    [Connector.py]
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2021-11-13 Moved wheel motors apart, added profile end caps
    [Mirrormotor-body-mount.SLDPRT, axle-mount-bottom.SLDPRT, axle-mount-top.SLDPRT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]
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2021-11-14 Fixed teleop config, increased acceleration limits
    [diff_drive_controller.yaml]
2021-11-14 Fixed diff drive acceleration config types
    [diff_drive_controller.yaml]
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
